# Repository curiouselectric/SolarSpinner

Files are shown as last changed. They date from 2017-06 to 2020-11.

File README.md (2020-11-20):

# SolarSpinner
Solar powered Motor controller with circuit diagram, PCB and code.
This is based upon the ATTiny85, with code written and uploaded via the Arduino IDE.

This design is for a reporgrammable unit which can do different tasks, powered by a small solar PV cell and an ultra-capacitor.

The unit has an LED output, a Motor control output and a Piezo buzzer output.

## Files Included:

* PCB files (KiCAD required)
* Software (Arduino IDE with ATTiny extension required)
* Hardware (DXF files)
* Instructions (for the final device!)

## Pin out#

ATTiny85 Arduino Pins:

|IC Pin: |Arduino Ref: | Attached:  |
|---|---|---|
|1 | 5/A0/RST  | |
|2 | 3/A3 | Vsolar |
|3 | 4/A2 | Vcap |
|4 |  GND | |
|5 | 0 - PWM | Piezo |
|6 | 1 - PWM | Motor |
|7 |  2/A1 | LED |
|8 | +Supply | |

## Software Modes

Note: There are only 3 sleep modes for the ATTiny25/45/85

These are: IDLE, ADC power down and Power-Down

If we want to use the PWM to give an output then we need to use IDLE.

See datasheet for more details: http://www.atmel.com/images/atmel-2586-avr-8-bit-microcontroller-attiny25-attiny45-attiny85_datasheet.pdf

### Motor Control

This runs a motor using stored power in the capacitor.
When the Vcap voltage is above a certain amount the motor is run unit the voltage drops.

Control is as follows:

* Wake up on Watch Dog Timer (every set time (0.5 or 1 second)
* If Vcap > Vhigh start with PWM = 255 (fully on) & set motor = ON
* If Vcap < Vhigh & motor is ON then reduce the PWM from 255 by 1 (down to a minimum speed)
* If Vcap < Vlow then switch off the unit & set motor = OFF
* Enter sleep

### LED Nightlight

Automatically switches on an LED when the solar input is low. This will run until the capacitor voltage is too low.

Control is as follows:

* Wake up on Watch Dog Timer (every set time (0.5 or 1 second)
* If Vcap > Vhigh && Vpv < Von setpoint then LED = ON
* If Vpv > V off set point then LED = OFF
* If Vcap < Vlow then switch off LED = OFF
* Enter sleep

### Solar Cricket

'Chrips' a noise (using a piezo element attached to the motor connections) when there is sunlight. Rate and pitch of chirping depends upon solar input. Lower solar = lower pitch chirp and lower rate of chirp.
Control is as follows:

* Wake up on Watch Dog Timer (every set time (0.5 or 1 second)
* If Vcap > Vhigh start 'chirp'. 'chirp' frequency is set by Vpv
* 
* If Vcap < Vlow then switch off the unit & set motor = OFF
* Enter sleep

### Nighttime Cricket

'Chirps' a noise (using a piezo element attached to the motor connections) when the solar voltage is low (dark). Does this until the capacitor runs out.
Control is as follows:

* Wake up on Watch Dog Timer (every set time (0.5 or 1 second)
* If Vcap > Vhigh start with PWM = 255 (fully on) & set motor = ON
* If Vcap < Vhigh & motor is ON then reduce the PWM from 255 by 1 (down to a minimum speed)
* If Vcap < Vlow then switch off the unit & set motor = OFF
* Enter sleep

### Ultrasonic Bug Repeller

Some animals (cats, dogs, rats) and insects (mosquittos) respond to different ultrasonic frequencies of sound.
https://en.wikipedia.org/wiki/Electronic_pest_control
Some people question the effectiveness of this, so this is here for a bit of a trial, really - see what you think!

Control is as follows:

* Wake up on Watch Dog Timer (every set time (0.5 or 1 second)
* If Vcap > Vhigh start repller = ON
* If repeller = ON  then Set PWM = random time between 40-255
* If Vcap < Vlow then switch off the unit & set motor = OFF
* Enter sleep

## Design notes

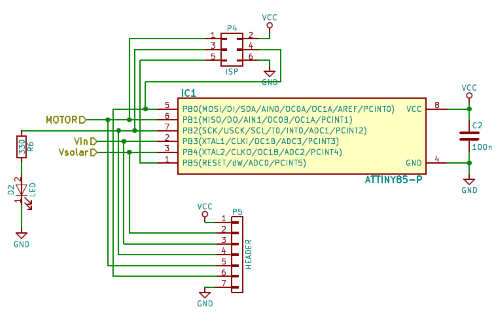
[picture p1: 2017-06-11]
SolarSpinner_Photos/Circuit3.png

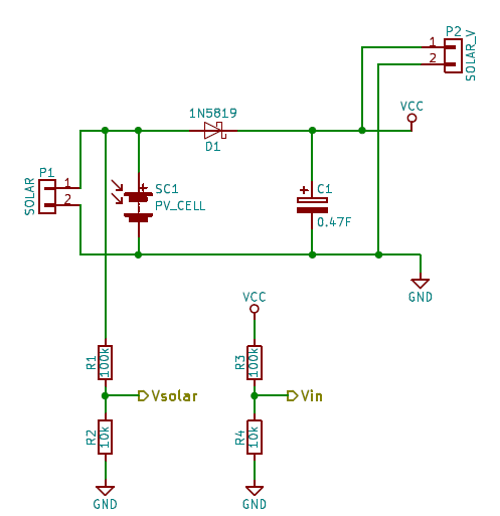
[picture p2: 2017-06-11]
SolarSpinner_Photos/Circuit1.png

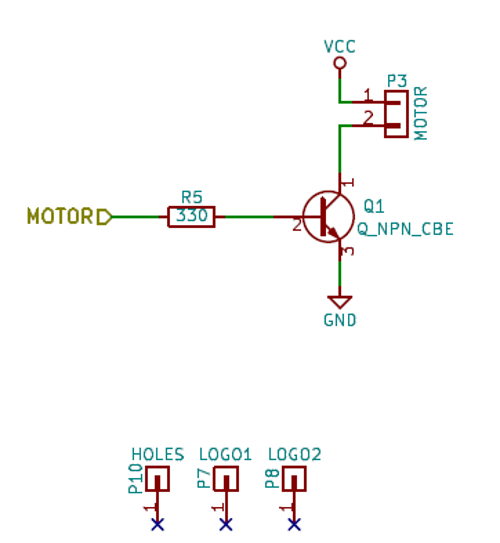
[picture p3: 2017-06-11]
SolarSpinner_Photos/Circuit2.png

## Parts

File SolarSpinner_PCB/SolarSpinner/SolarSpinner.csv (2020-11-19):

Reference | Value | Footprint | Datasheet | Supplier 1 | Supplier 1 Cost | Description | Manufacturer | Manufacturer Part No | Supplier 1 Part No
C1 | 0.47F | REInnovationFootprint:C_0_47F_SuperCap |  | Aliexpress | 0.4
SC1 | PV_CELL | REInnovationFootprint:PV_50x30mm_round |  | Aliexpress | 0.7 | 53x30mm 30mA 5V PV module
D1 | 1N5819 | REInnovationFootprint:TH_Diode_1 |  | RS | 0.03
P7 | LOGO1 | CuriousElectric3:CEC_Globe_10mm_FCU
P8 | LOGO2 | CuriousElectric3:TCEC_Words_13mm
P2 | SOLAR_V | matts_components:SIL-2_wide_lg_pad
IC1 | ATTINY85-P | REInnovationFootprint:DIP-8_300_ELL | http://www.farnell.com/datasheets/1744708.pdf | Farnell | 1.12 | 8 Bit uP 20MHz | ATMEL | ATTINY85-20PU | 1455162
C2 | 100n | matts_components:C1_wide_lg_pad |  | Rapid | 0.07
R3 | 100k | REInnovationFootprint:TH_Resistor_1 |  |  | 0.01
R4 | 10k | REInnovationFootprint:TH_Resistor_1 |  |  | 0.01
Q1 | BC547 | REInnovationFootprint:TO92-EBC_large_pad
R5 | 330 | REInnovationFootprint:TH_Resistor_1 |  |  | 0.01
P3 | MOTOR | matts_components:SIL-2_screw_terminal
P1 | SOLAR | matts_components:SIL-2_screw_terminal
P4 | ISP | REInnovationFootprint:ISP_3x2 |  |  | 0.05
R1 | 100k | REInnovationFootprint:TH_Resistor_1 |  |  | 0.01
R2 | 10k | REInnovationFootprint:TH_Resistor_1 |  |  | 0.01
P5 | HEADER | REInnovationFootprint:SIL-7_DIO
P10 | HOLES | REInnovationFootprint:PCB_Holes_40x50
R6 | 330 | REInnovationFootprint:TH_Resistor_1 |  |  | 0.01
D2 | LED | REInnovationFootprint:LED-5MM_larg_pad |  | Aliexpress | 0.1 | 5mm White LED ?

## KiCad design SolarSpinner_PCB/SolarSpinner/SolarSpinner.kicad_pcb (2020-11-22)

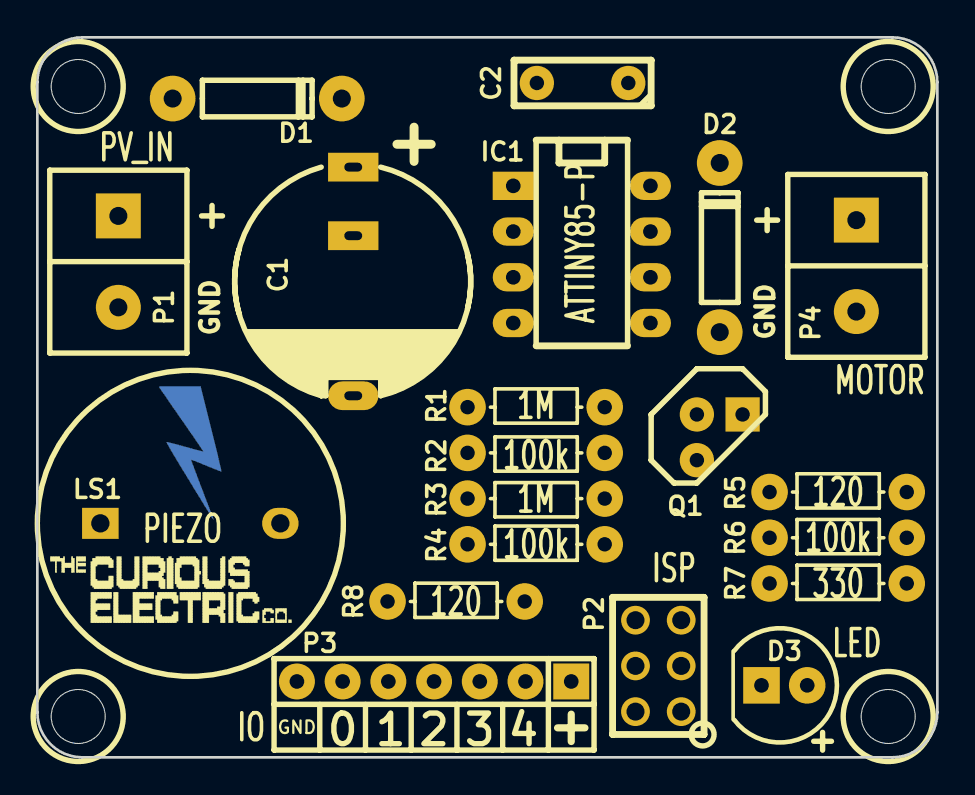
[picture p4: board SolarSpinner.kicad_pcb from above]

Board: 2 copper layers, 50.0 x 40.0 mm, 23 parts (0 on the bottom side), 13 nets, no tracks yet.

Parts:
C1: 0.47F; C_0_47F_SuperCap_2POS
C2: 100n; C1_wide_lg_pad_2
D1: 1N5819; TH_Diode_1
D2: 1N4001; TH_Diode_1
D3: LED; TH_LED-5MM_larg_pad
IC1: ATTINY85-P; DIP-8_300_ELL
LS1: PIEZO; TH_PIEZO_17x7
P1: PV_IN; SIL-2_screw_terminal
P2: ISP; ISP_3x2
P3: IO; SIL-7_DIO
P4: MOTOR; SIL-2_screw_terminal
P5: HOLES; PCB_Holes_40x50
P6: LOGO1; 2019_011_16_CuriousElectricCompany_Logo_Round_Logo_No_words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
P7: LOGO2; TCEC_Words_13mm
Q1: BC547; TO92-EBC_large_pad
R1, R3: 1M; TH_Resistor_1
R2, R4, R6: 100k; TH_Resistor_1
R5, R8: 120; TH_Resistor_1
R7: 330; TH_Resistor_1

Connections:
/LED: IC1.7, P2.3, P3.4, R7.1
/MOTOR: IC1.6, P2.1, P3.5, R5.1
/PIEZO: IC1.5, P2.4, P3.6, R8.1
/Vin: IC1.2, P3.3, R3.1, R4.2
/Vsolar: IC1.3, P3.2, R1.1, R2.2
GND: C1.2, C2.2, D3.1, IC1.4, LS1.2, P1.2, P2.6, P3.7, Q1.3, R2.1, R4.1, R6.1
unnamed: D1.2, P1.1, R1.2
unnamed: D2.1, P4.2, Q1.1
unnamed: D3.2, R7.2
unnamed: IC1.1, P2.5
unnamed: LS1.1, R8.2
unnamed: Q1.2, R5.2, R6.2
VCC: C1.1, C2.1, D1.1, D2.2, IC1.8, P2.2, P3.1, P4.1, R3.2

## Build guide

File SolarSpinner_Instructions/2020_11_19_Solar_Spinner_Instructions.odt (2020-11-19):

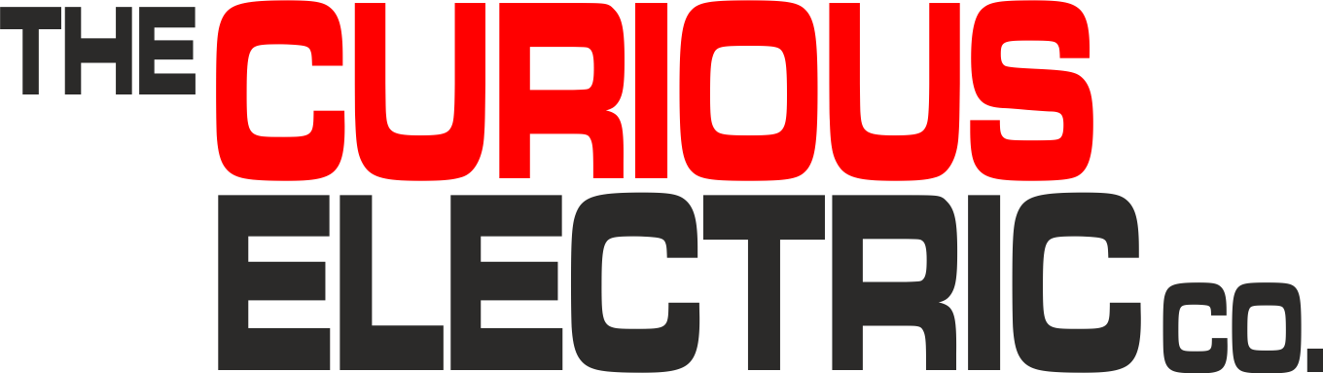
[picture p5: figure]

| Solar Charger Kit Instructions

Date: | 15/09/17 | Version: | 1.0 | By: | Matt Little

| Build your own solar charger! This unit has a USB output to recharge phones and other small devices. There are two 1Wp solar panels which recharge a bank of three AA batteries. A DC-DC converter ensures regulated 5V for the USB connector output. This is a reasonably simple kit which requires some soldering and a few fiddly connections. It should take 1-2 hours to build. Not suitable for under 12 years old.

# Parts included:

| | | Laser-cut Enclosure | | | 3 x AA rechargeable batteries
1W Solar PV Modules
| | | | | | | | Battery Holder
DC-DC Converter
| | | | | | | | 7 x M3 Hex spacers
PCB | | | | | | | | 7 x M3 6mm 7 x M3 8mm
| | | | | | | | Sticky Pads
Wire
| | Diode 1N4001 | | | | Switch + 2 x M2.5 screws

# Enclosure Parts:

Top 1 | | Front
Top 2
Top 3 | | Back
Bottom 1
Bottom 1
Bottom 1 | | Switch Holder

# Parts list:

Item | Quantity
DC DC Converter | 1
Diode | 1
PCB | 1
Switch | 1
M2 Machine screws 10m long | 2
M3 Machine screws 6mm long | 7
M3 Machine screws 8mm long | 7
M3 Threaded Hex spacers 8mm long | 7
3 x AA Battery Holder | 1
AA NiMH Rechargable Batteries | 3
1Wp Solar PV Units. 5V max out. | 2
Wire – Red and Black | length
Laser-cut enclosure (9 pieces) 3mm Ply | 1
Double sided sticky pads | 3

# Tools required:

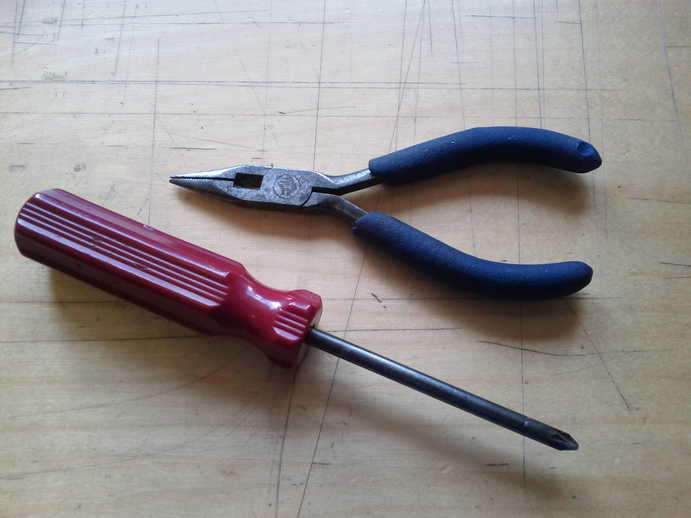
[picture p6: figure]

Posi-drive Screwdriver
| | Long-nosed Pliers
| | Soldering Iron
| | Solder
| | Side cutters
| | (not shown)

Instructions:

Step: 1 | Push out laser-cut parts
Sometimes not all the small laser-cut pieces have been removed. These can be pushed out using the point of a screwdriver. Only slight force should be required.

Step: 2 | Solder diode
| | Solder the diode onto the PCB. This is the only component on the PCB. Ensure it is the correct orientation – the grey line on the diode body should go next to the thicker white line on the PCB. Solder and cut off the wire ends.

Step: 3 | Add switch
Fix the switch to the wooden switch older with the two M2.5 screws. Cut two pieces of wire 50mm long (one red/one black). Solder them to two tabs on the switch – choose two on one row – the middle tab and the one near the ON side, marked with a small circle.

Step: 4 | Fit Solar PV Cells

Take the two solar PV units.

Lie them flat next to each other with the + to the same side and the – to the other side.

Cut 2 x 70mm long pieces of wire (one red, one black).

Solder these to the tabs on the edge of the PV units.

The red wire will connect the +'s of both modules.

The black wire will connect the -'s of both modules.

Cut 2 x 100mm long pieces of wire (one red, one black).

Put some solder onto the two middle pads of one of the PV units.

Solder the red wire to the + pad and the black wire to the – pad.

We want the wires to be soldered so the 'stand-up' so the come out of the back of the module.

These wires are fed through the wooded 'front' piece.

Ensure that the wires go through from the front of the unit (ensure the slot is on the left hand side). The front has the better quality side, with no laser cutter burn marks.

Use two of the sticky pads, each cut in half, to stick to the back of the PV units.

Then stick the two PV units to the front of the unit. Ensure they are well aligned, straight and next to each other.

We suggest doing a practice run, before removing the protective cover of the sticky pads.

You can also use silicone sealant to do this.

Step: 5 | Solder DC-DC
Cut 2 x 70mm pieces of wire (one red and one black). Solder the red wire to the +ve connection and the back wire to the -ve.

Step: 6 | Solder to PCB
| | Solder each part to the connector PCB. The red wire always goes to the + hole. There are four things to connect to the PCB: Solar PV units DC-DC Converter Switch Battery pack The battery holder already has wires attached. Be careful with your soldering. Make sure that there are no solder 'bridges' between the pads on the PCB. Cut any excess wire from the soldered side of the PCB. You can insert the batteries here and check that the light on the DC-DC converter turns on when the switch is towards the ON position. If the switch action is reversed, then just unscrew the switch and rotate it.

Step: 7 | Fit plastic spacers
Now we will put it all together in the enclosure. From the front wood piece (with the PV units stuck to it), use seven of the black M3 6mm, one through each hole and screw into the hex plastic spacer. Do not tighten these fully, as they will need to be aligned.

Step: 8 | Add level 1
| | Take the base unit marked '1'. Flip it around so the '1' is facing the front. Fit it around the PV wires coming from the back of the front piece. Rotate the hex spacers slightly to align with the hexagonal holes. Fit the DC-DC converter into the slot on the left hand side. Ensure the USB socket faces the bottom of the unit. Fit the switch (facing outwards) into the slot.

Step: 9 | Add level 2
Take the bottom piece marked '2'. Flip it around so the '2' faces the front. The wires from the DC DC converter and the solar PV feed through to the slot at the top of piece '2'. Ensure no wires are trapped between layers. The wire from the battery pack comes in from the middle slot.

Step: 10 | Add level 3
| | Take the bottom piece marked '3' and flip it around. Ensure the wires are not trapped and fit through the holes. The PCB and the excess wires need to be carefully fitted in to the space behind the switch. If your wires are too long then this can be fiddly.

Step: 11 | Add back
Fit the back to the unit. The logo shows to the back of the unit. Fit the battery holder through the hole. Ensure no wires are trapped between layers. Use 5 x M3 8mm silver screws to fasten the back.

Step: 12 | Add top hanger
| | The hanging section can be built up then inserted into the top of the charger main unit. Do this by placing 1 on top of 2 on top of 3. Piece number 2 should be in the middle, with 1 and 3 on either side. Insert a plastic spacer into the hex hole. Carefully push into the top of the unit. Do this one side at a time. Use 2 x M3 6 mm long machine screws for the front of the unit. Use 2 x M3 8mm long machine screws for the back of the unit.

Step: 13 | Add battery holder
With the remaining sticky pad, stick this to the BACK of the battery holder. The front has a removable panel for access to the batteries. The back does not and has a couple of small cut out holes (see photo). Carefully align the battery holder so that the top (without wires) is pushed up against the top of the charger. This leaves a small gap at the bottom so that the back can be removed and the batteries replaced.

Step: 14 | Fit batteries
| | Remove the back cover of the AA battery holder. Do this by pushing down the removable black plastic panel. There might be a small screw – this needs to be removed to gain access to the batteries. Insert the 3 x AA batteries. ENSURE CORRECT POLARITY! Replace the back cover and insert the small screw, if you will not need access to the batteries often.

Step: 15 | Test working
The unit is nearly done. You want to test that it is working by pushing the switch to the ON position. There should be a small red glow from behind the USB connector. This means the DC/DC converter is working. The solar panels will recharge the batteries whenever it is in the sun (does not matter the position of the switch). Leave the unit switched OFF if nothing is plugged into the USB port.

Step: 16 | Build is finished!

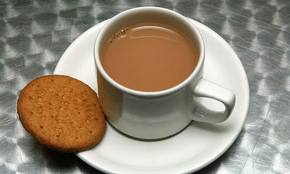
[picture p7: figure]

| | Remove the protective plastic cover from the solar PV units. Leave your new creation in the sun to recharge. Have a nice cup of tea. Use a piece of string or wire through the two holes at the top and it can be hung from a hook.

Note: This unit is NOT waterproof. Do NOT leave outside if it will get wet.

Note: The weather and available sunlight is variable, so there are no definite rules about recharging times.

If outside on an average UK summers day the batteries will be fully charged in one day.

If outside on an average UK winters day then the batteries will be fully charged in 2-3 days.

If used behind a window, the glass will affect the available sunlight and increase the recharge times by a factor or around 50%.

This kit has been designed and produced by:

The Curious Electric Company

hello@curiouselectric.co.uk

www.curiouselectric.co.uk

Hopkinson Gallery, 21 Station Street, Nottingham, NG2 3AJ

# Contact details:

We would like you to be happy with this kit. If you are not happy for any reason then please contact us and we will help to sort it out.

Please email hello@curiouselectric.co.uk with any questions or comments.

Please tweet us at @curiouselectric

If any parts are missing from your kit then please email hello@curiouselectric.co.uk with details, including where the kit was purchased.

More technical information can be found via www.curiouselectric.co.uk

# Circuit Schematic:

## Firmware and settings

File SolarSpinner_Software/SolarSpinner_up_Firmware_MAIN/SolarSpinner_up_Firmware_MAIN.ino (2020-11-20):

/*

  Solar Spinner - Solar ATTiny85 Motor Control Unit
  with AtTiny85 @ 1Mhz  (??)

  By:   Matt Little
  Date: 19/11/2020
        heelo@curiouselectric.co.uk

  This code sends the ATTiny85 to sleep using the watchdog timer
  The Capacitor voltage is checked and if >VOLT_HIGH then the unit will switch on
  Until Capacitor voltage < VOLT_LOW

  The speed of the motor is set with a random PWM?

*/

#include "config.h"
#include "functions.h"

// Program variables
volatile boolean f_wdt = 1;
float Vpower;
float Vsolar;
float Vpower_previous;
int motorPWM = 0; // This is the motor PWM value
boolean LEDstate = LOW;
boolean motorRun = LOW;


void setup()
{
  pinMode(PIN_LED, OUTPUT);
  pinMode(PIN_MOTOR, OUTPUT);
  setup_watchdog(5); // approximately 0.5 seconds sleep
  analogReference(INTERNAL);
  randomSeed(analogRead(PIN_VCAP)); // Sets up a random seed
}

void loop() {

  if (f_wdt == 1)
  {
    // Woken up on Watch Dog Timer
    f_wdt = 0;     // reset flag

    Vpower = return_voltage(PIN_VCAP);
    Vsolar = return_voltage(PIN_VPV);

    if (Vpower > VOLT_HIGH)
    {
      // Set motor running
      motorRun = HIGH;
      motorPWM = 255;
    }
    else if (Vpower < VOLT_LOW)
    {
      //stop motor
      motorRun = LOW;
      digitalWrite(PIN_MOTOR, LOW);     // Switch OFF motor
      LEDstate = LOW;
      digitalWrite(PIN_LED, LEDstate);  // Switch OFF led
    }
    else if (Vpower < Vpower_previous)
    {
      motorPWM--;   // Ramp down the motorPWM
      if (motorPWM <= 0)
      {
        motorPWM = 0;
      }
    }
    else if (Vpower > Vpower_previous)
    {
      motorPWM++;   // Ramp down the motorPWM
      if (motorPWM > 255)
      {
        motorPWM = 255;
      }
    }

    Vpower_previous = Vpower;

    if (motorRun == HIGH)
    {
      analogWrite(PIN_MOTOR, motorPWM);     // Set Motor to run at PWM level
      //digitalWrite(PIN_MOTOR, HIGH);      // Switch ON motor
      LEDstate = !LEDstate;
      digitalWrite(PIN_LED, LEDstate);    // let led blink
      delay(5);
    }

    //pinMode(PIN_LED, INPUT); // set all used port to intput to save power
    //pinMode(PIN_MOTOR, INPUT); // set all used port to intput to save power
    system_sleep();
    //pinMode(PIN_LED, OUTPUT); // set all ports into state before sleep
    //pinMode(PIN_MOTOR, OUTPUT); // set all ports into state before sleep
  }
}

// Watchdog Interrupt Service / is executed when watchdog timed out
ISR(WDT_vect) {
  f_wdt = 1; // set global flag
}

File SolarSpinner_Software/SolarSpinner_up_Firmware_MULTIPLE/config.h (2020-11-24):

#pragma once

//#define F_CPU 8000000  // This is used by delay.h library
#define F_CPU 1000000  // This is used by delay.h library

#include <avr/sleep.h>
#include <avr/wdt.h>
#include <stdlib.h>
#include <EEPROM.h>        // For writing values to the EEPROM
#include <avr/eeprom.h>    // For writing values to EEPROM
#include <avr/io.h>        // Adds useful constants
#include <util/delay.h>    // Adds delay_ms and delay_us functions
#include <Arduino.h>

#ifndef cbi
#define cbi(sfr, bit) (_SFR_BYTE(sfr) &= ~_BV(bit))
#endif
#ifndef sbi
#define sbi(sfr, bit) (_SFR_BYTE(sfr) |= _BV(bit))
#endif

// Pin Definitions

#define PIN_BUZZER  0
#define PIN_MOTOR   1
#define PIN_LED     2       // Cant do PWM on  D2.
#define PIN_VCAP    A3      // D3
#define PIN_VPV     A2      // D4


// Control parameters
#define VOLT_LOW    2.0
#define VOLT_HIGH   4.5
#define MAX_SPEED   75
#define MIN_SPEED   25

#define MODE        0       // This sets what the unit does: 0 = solar motor, 1 = solar cricket (day) 2 = solar cricket (night)

#define WDT_MODE    5       // 0=16ms, 1=32ms,2=64ms,3=128ms,4=250ms,5=500ms
                            // 6=1 sec,7=2 sec, 8=4 sec, 9= 8sec

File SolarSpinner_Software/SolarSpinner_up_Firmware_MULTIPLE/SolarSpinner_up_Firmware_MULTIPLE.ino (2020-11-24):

/*

  Solar Spinner - Solar ATTiny85 Motor Control Unit
  with AtTiny85 @ 1Mhz  (??)

  By:   Matt Little
  Date: 19/11/2020
        heelo@curiouselectric.co.uk

  This code sends the ATTiny85 to sleep using the watchdog timer
  The Capacitor voltage is checked and if >VOLT_HIGH then the unit will switch on
  Until Capacitor voltage < VOLT_LOW

*/

#include "config.h"
#include "functions.h"

// Program variables
volatile boolean f_wdt = 1;
float Vpower;
float Vsolar;
float Vpower_previous;
int motorPWM = 0; // This is the motor PWM value
boolean LEDstate = LOW;
boolean modeRun = LOW;
int local_mode;

void setup()
{
  pinMode(PIN_LED, OUTPUT);
  pinMode(PIN_MOTOR, OUTPUT);
  pinMode(PIN_BUZZER, OUTPUT);

  setup_watchdog(WDT_MODE); // approximately 0.5 seconds sleep
  analogReference(INTERNAL);
  //randomSeed(analogRead(PIN_VCAP)); // Sets up a random seed
  local_mode = MODE;
}

void loop() {

  if (f_wdt == 1)
  {
    // Woken up on Watch Dog Timer
    f_wdt = 0;     // reset flag

    Vpower = return_voltage(PIN_VCAP);
    Vsolar = return_voltage(PIN_VPV);

    switch (local_mode)
    {
      case 0:
        // In this case we are in solar motor mode
        if (Vpower > VOLT_HIGH)
        {
          // Set motor running
          modeRun = HIGH;
          motorPWM = MAX_SPEED;
        }
        else if (Vpower < VOLT_LOW)
        {
          // Too low - switch off everything and go to sleep!
          modeRun = LOW;
          analogWrite(PIN_MOTOR, 0);     // Set Motor to run at PWM level
          digitalWrite(PIN_LED, LOW);  // Switch OFF led
        }
        else if (Vpower < Vpower_previous)
        {
          motorPWM--;   // Ramp down the motorPWM
          if (motorPWM <= MIN_SPEED)
          {
            motorPWM = MIN_SPEED;
          }
        }
        else if (Vpower > Vpower_previous)
        {
          motorPWM++;   // Ramp down the motorPWM
          if (motorPWM > MAX_SPEED)
          {
            motorPWM = MAX_SPEED;
          }
        }
        if (modeRun == HIGH)
        {
          analogWrite(PIN_MOTOR, motorPWM);     // Set Motor to run at PWM level
          flash(1, PIN_LED);
        }
        Vpower_previous = Vpower;     // Store the prvious power value for next time analysis
        break;

      case 1:
        // In this case we are in solar cricket mode (daytime)
        // This will chirp at a frequency related to the PV voltage
        if (Vpower > VOLT_HIGH)
        {
          modeRun = HIGH;
          //chirpHigh(PIN_BUZZER);
        }
        else if (Vpower < VOLT_LOW)
        {
          // Too low - switch off everything and go to sleep!
          modeRun = LOW;
          digitalWrite(PIN_MOTOR, LOW);     // Switch OFF motor
          digitalWrite(PIN_LED, LOW);  // Switch OFF led
        }
        
        if (Vsolar < Vpower_previous)
        {
          chirpLow(PIN_BUZZER);
        }
        else if (Vsolar > Vpower_previous)
        {
          chirpHigh(PIN_BUZZER);
        }
        if (modeRun == HIGH)
        {
          flash(2, PIN_LED);
        }
        Vpower_previous = Vsolar;     // Store the prvious power value for next time analysis
        break;  
    }

    //pinMode(PIN_LED, INPUT); // set all used port to intput to save power
    //pinMode(PIN_MOTOR, INPUT); // set all used port to intput to save power
    system_sleep(local_mode);
    //pinMode(PIN_LED, OUTPUT); // set all ports into state before sleep
    //pinMode(PIN_MOTOR, OUTPUT); // set all ports into state before sleep
    //pinMode(PIN_BUZZER, OUTPUT);
  }
}

// Watchdog Interrupt Service / is executed when watchdog timed out
ISR(WDT_vect) {
  f_wdt = 1; // set global flag
}

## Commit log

2017-06-11 Initial comit
    [SolarSpinner.kicad_pcb, SolarSpinner.sch]
2017-08-18 Updated PCB
2017-08-18 Updated PCB. New Gerber
    [SolarSpinner-B.Cu.gbr, SolarSpinner-B.Mask.gbr, SolarSpinner-B.SilkS.gbr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]
2020-11-19 Large update of tests
    [SolarSpinner.csv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]
2020-11-20 small update
    [SolarSpinner.sch]
2020-11-20 Code Update for different functions
    [SolarSpinner.kicad_pcb, SolarSpinner.sch]
2020-11-22 Update of PCB and schematic
    [SolarSpinner.kicad_pcb, SolarSpinner.sch]
